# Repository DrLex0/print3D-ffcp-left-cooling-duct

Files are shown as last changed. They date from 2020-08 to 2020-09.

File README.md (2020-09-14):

# FlashForge Creator Pro left single extruder fan duct
*Cooling duct for the left extruder of the FlashForge Creator Pro and similar 3D printers (formerly thing:2436915)*

### License
[Creative Commons - Attribution](https://creativecommons.org/licenses/by/4.0/)

### Attribution
This is a remix of my own [‘FlashForge Creator Pro front dual fan duct’](https://github.com/DrLex0/print3d-ffcp-dual-cooling-duct).

### Gallery

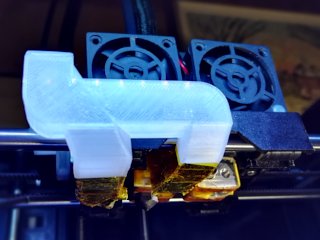
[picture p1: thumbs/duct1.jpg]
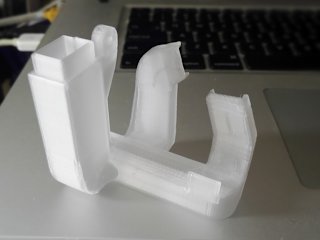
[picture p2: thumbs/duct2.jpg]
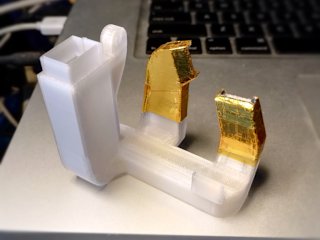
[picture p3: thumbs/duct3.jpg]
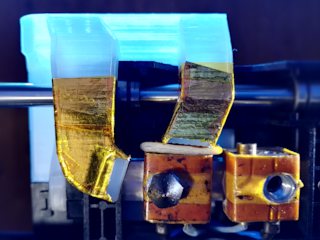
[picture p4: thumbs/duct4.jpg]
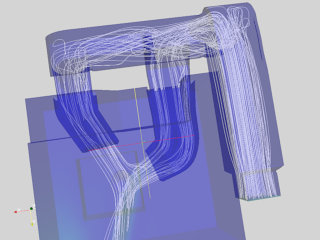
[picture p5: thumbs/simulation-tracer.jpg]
Simulation
[🔎](images/duct1.jpg) [🔎](images/duct2.jpg) [🔎](images/duct3.jpg) [🔎](images/duct4.jpg) [🔎](images/simulation-tracer.png)

## Description and Instructions

This is the single-extrusion alternative to my [dual duct](https://github.com/DrLex0/print3d-ffcp-dual-cooling-duct). I only do a dual extrusion about once every 100 prints, and I figured it is a bit pointless to have the dual duct blow air at the inactive (and usually unscrewed) nozzle all the time. It makes more sense to also direct this air at the active nozzle. By blowing air from two directions, this design reduces the ‘shadow’ problem both the stock duct and my dual duct suffer from, and cools more equally from all sides. If you're only going to print with one extruder, this duct will give you the best quality. Of course this does not make the dual duct obsolete: you still need it to get proper cooling on dual extrusions.

Mind that the shadow problem is not completely eliminated. Overhangs at the rear and right will still be cooled less effectively because the air cannot reach their undersides. One way to work around this is to print extra walls behind such overhangs to reflect the airflow back towards them. In most cases this will be unnecessary however, but keep it in mind for those prints that need to be really perfect.
(Someday I might try to update the design to have opposite exhausts for symmetrical cooling but this will obviously require big changes.)

This duct unfortunately is not plug-and-play. You must read the **Using** section. If you don't, your prints will likely fail, you have been warned.

Quite a bit of time and effort went into designing this. If you want to show some appreciation, [there are some tipping options on my site](https://www.dr-lex.be/about/#contact).

This duct has not been merely designed in a wet-finger guessing way. It has been run through several dozens of iterations, the last of which were validated with computer simulations. See the ‘How I Designed This’ section for more details.

### Pre-printing: check nozzle height

There are two models to choose from. To determine which one you need, do the following test. *Move the bed against the nozzles (as if you are going to use the levelling sheet), then bring the carriage forward and measure the distance between the bed surface and the cradle as shown in the photo.*

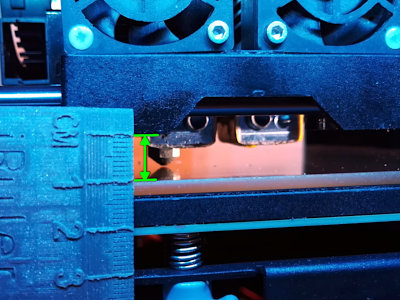
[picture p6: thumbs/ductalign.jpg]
Alignment
[🔎](images/ductalign.jpg)

The regular duct model is designed to be optimal if this distance is **10 mm,** which is normally the case on a standard FFCP. It should also be this way if you aligned the nozzles with [this leveler](https://www.thingiverse.com/thing:1582720).

The ‘x1’ model is for when this distance is **11 mm.** This is likely the case if you installed Micro Swiss all-metal hot-ends and followed their instructions exactly.

If your nozzles are at a considerably different height, you should consider realigning them. If that's not possible, your only option is to modify the duct model.

### Printing

As with the dual duct or any duct whatsoever, you must print this in a **heat-resistant material** because it is very close to the heater block, moreover this duct has even more material near the heated bed. Do *not* print it in PLA. I recommend **ABS** although even that may not be sufficiently heat-resistant on its own during ABS or PETG prints. If you are able to print in polycarbonate, it is probably the best option if you often print with the bed above 100°C or the extruders at 230°C or more. An ABS printed duct will do fine however if you add extra insulation (see *post-printing* section).

This is designed to be printed with an extrusion width of 0.4 mm such that all structures have at least 2 perimeters. The recommended layer height is 0.2 mm. Thinner layers will of course also be OK, and might be beneficial for strength when printing in ABS.

Same remark as for the dual duct: do not enable supports, they could block the inner passages. The model is designed such that it will print well without supports in the orientation of the STL file, i.e., with the inlet pointing upwards.
I recommend enabling cooling while printing the top layer of the main vent and the upper tip of the left exhaust (for this purpose the stock duct should suffice).
Infill doesn't matter much if your slicer is configured to always print small areas solid. If unsure, set infill to 100% for the entire print.

### Post-Printing

**Preparing the duct for mounting**

You should ream the little hole next to the mounting screw hole with a 2 mm drill bit. Otherwise you'll probably have a hard time mounting the duct onto the carriage.

**Protecting the duct against heat**

Even if you printed the duct in ABS, it still is very close to the heater block and the exhausts *will* deform if the duct is exposed to high temperatures for more than just a few minutes while the fan is off or running at very low speed. If the exhausts deform, the duct will no longer work optimally. You should therefore consider applying some thermal insulation to the exhausts, especially if you print with ABS or PETG.

As shown in the photos, I use some NASA-style insulation that consists of a layer of self-adhesive aluminium foil, with a layer of kapton tape on top. To be really sure, I applied this twice at the tips of the exhausts. It is time-consuming to apply this but is well worth it because it has proven to be extremely effective. If you have only one of those materials, I believe a few layers of just aluminium or just kapton will also do the trick.

There are a few cases in which you might get away without insulation:
* If you're only going to print PLA or other filaments that do not require extruder temperatures above 210°C and no bed temperatures above 80°C.
* If you always enable the cooling fan at (near-)maximum speed. This will keep the duct itself cooled and it won't deform. However if you only enable the fan after the first few layers (as you should), then you still risk damaging the duct when printing something large because the duct will remain uncooled during those long first layers.
* If your heater blocks have much better thermal insulation than mine.

### Installing
A thin strip of rubber (like a piece of bicycle tire) under the little mounting tab can help to avoid that the duct vibrates and rattles.

If you have an older printer and yet have to install the blower fan, you may need to print the [fan mounting bracket](https://www.thingiverse.com/thing:2086927) first.

### Using
First of all if you're going to do a long print with the fan disabled entirely, remove the duct to avoid that it will deform, especially if you're printing at very high temperatures, e.g. polycarbonate. Even if you applied thermal insulation, you should still remove the duct if unused during long prints.

Next, very important: don't just print and try to use this duct, it unfortunately is not that simple. **This duct is almost unusable if you cannot control fan speed.** You risk getting very poor layer adhesion in the lower part of your print, and fast-printed parts like infill may detach already during printing. In other words, your print will fall apart. To avoid this, you must reduce fan speed in a specific manner. Unfortunately **fan speed cannot be controlled on an unmodified FFCP,** which I find the largest shortcoming of this printer by far. Modifications are required, below I explain how you can get variable fan speed after all.

Due to effects described below (see ‘Background info’ if you're interested), you must:
* only enable the fan after the second or third layer,
* start out with the fan running at no more than 20% speed,
* gradually increase fan speed over the course of the first few millimeters of the Z-axis until the desired maximum (in my case 50% is usually more than enough).

Being able to control fan speed is the only practical way to get optimal cooling with this duct (actually with any duct for that matter). Variable speed is also essential for getting good results with filaments like PETG, which require a tiny bit of cooling for best results. You may also be surprised to hear that I always enable the fan on ABS prints albeit at very low speed, which does improve quality without ruining layer adhesion. Also, after installing an all-metal hot-end with hardened steel nozzle, I noticed I need much less cooling which made it essential to be able to throttle the fan.

### How to obtain variable fan speed
Your software might make it seem as if you can vary the speed of the fan, but this is a *lie.* None of the printers that use the MightyBoard design like the FFCP and clones, can control fan speed without modifications. The MightyBoard can only toggle its EXTRA output on and off, hence ramping up the fan won't be possible.

Some options:
* Simplest is to install a [hardware PWM controller](https://www.thingiverse.com/thing:2095862) in between the printer motherboard and the cooling fan. This isn't complicated and the only (optional) permanent modification you need to make to your printer is to drill two tiny holes. You can use an analog controller like the one shown there, or a microcontroller like an Arduino with PWM capable output and a 24V MOSFET to drive the fan. This solution is still cumbersome because you will need to babysit every print at least during its first few layers to slowly ramp up the fan speed.
* Better is to use my [MightyVariableFan system](https://github.com/DrLex0/MightyVariableFan), which will result in fully automatic fan speed control that reacts to G-code fan speed commands with high accuracy. Installing it is more work than mounting a single circuit board, but once you've got it running you will never want to go back.
* Install a recent build of the Sailfish firmware that has the software PWM feature. Speed cannot be changed however during a print and it does not respond to speed arguments in the G-code, making it mostly useless. A pull request exists that allows to build a custom firmware which is able to respond to fan speed commands in G-code, but this can only work if you also compile a custom build of the GPX converter and somehow manage to squeeze Sailfish-compatible G-code with variable fan speeds out of your slicing software. And when you have done all this, the timing of the fan speed changes will still be awful.

**Possible workarounds that do not require a PWM controller**

If you don't want to do the effort to add PWM but still want to use this duct, there are some fallbacks that might avoid total disaster, although they are all inferior to varying the fan speed.

* Simplest is to just stick with the [dual duct](https://github.com/DrLex0/print3d-ffcp-dual-cooling-duct).
* Print much hotter, slowly, and in thin layers to reduce the risk of layer delamination.
* To counteract the typical extruder temperature undershoot when the fan activates at lower layers, you could boost extruder temperature by 10°C about 10 seconds before the fan will engage. In theory this should put the extruder is in its heating regime when the blast of cold air hits it, and the undershoot should be reduced or eliminated. You may then gradually reduce extruder temperature again until the print is about 4 mm tall, but you should keep the temperature higher than when printing without fan. This is obviously cumbersome because you will either have to manually fiddle with the LCD menu to do this, or write a post-processing script to insert extra M104 commands in your G-code at the right places.
* Make a hole in the side of the duct to lower the exhaust pressure. You could use tape to vary the size of this hole hence vary airflow in a clumsy manner. Of course this doesn't avoid the undershoot problem and trying to vary the airflow during a print will be challenging to say the least.

## How I Designed This

### SimScale / OpenFOAM
I considered simulating the duct in OpenFOAM but its learning curve is a bit too steep for something I will only be using once or twice. Therefore I first tried the same trial-and-error methods as for the dual duct. These however proved ineffective: the two interacting airflows made the windmill unusable; blowing onto a water surface or a layer of dry sand was also pointless because these methods constrain the test to a 2D surface. (By the way, be extremely careful if you would ever cover the glass bed in your printer with sand. Due to static charge build-up, the sand is likely to jump upwards at the moment you remove the glass plate. It is a very cool physics demonstration but getting the sand out of all the nooks and crannies of your printer is not very cool.)

In the end I did simulate the duct using [SimScale](https://www.simscale.com/), which offers a web interface on top of OpenFOAM for CFD simulations, so this eliminates most of the learning curve. Moreover it is entirely free for public community projects (with a simulation time budget of 3000 hours). You can find the public project [here](https://www.simscale.com/projects/DrLex/ffcp_left_extruder_cooling_duct/).
I ended up performing some 15 different simulations. I couldn't imagine printing and manually testing all those prototypes, so the simulations proved invaluable. I did have some problems getting the STL model imported but in the end I found out how to properly do it, and I can conclude that SimScale is really great.

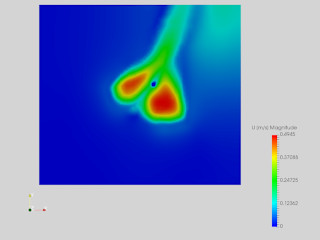
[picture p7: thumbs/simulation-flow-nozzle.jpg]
Simulation 1
[🔎](images/simulation-flow-nozzle.png)

*Airflow velocity around the tip of the nozzle. It is impossible to get a perfectly uniform flow field with only two exhausts, but this is about the best I could get within the constraints of this design.*

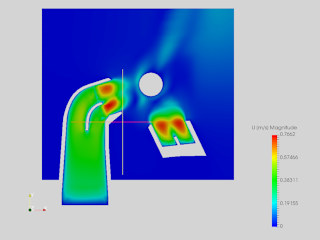
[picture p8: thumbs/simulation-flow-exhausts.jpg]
Simulation 2
[🔎](images/simulation-flow-exhausts.png)

*Flow in the exhausts. Getting this well-balanced was not trivial.*

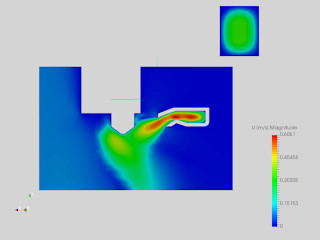
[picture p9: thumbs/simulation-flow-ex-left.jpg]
Simulation 3
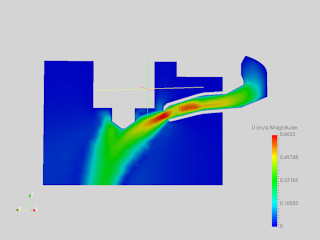
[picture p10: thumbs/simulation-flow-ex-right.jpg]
Simulation 4
[🔎](images/simulation-flow-ex-left.png) [🔎](images/simulation-flow-ex-right.png)

*Flow cross-sections of the left and right exhausts.*

### Validation

The following photos show a comparison of my 55° [mushroom test](https://www.thingiverse.com/thing:2005832) on a PLA print between this duct, the v6 dual duct, and the stock duct. The result from the stock duct looks more decent than what I expected from watching it being printed: it was curling up so badly at times that I feared I would need to abort the print. Somehow the upper layers managed to push down the curls again, but it still looks ugly. Even despite the fact that this was tested with the first version of this new duct which was not anywhere as good as the latest version, the result shows almost no deformations and it has a near-flat top surface. (Note: you won't be able to get this kind of result with the stock nozzles, especially not if they have been worn out. This was printed with a more pointy Micro Swiss hardened steel nozzle which allows to print steeper overhangs than a nozzle with a flat underside.)

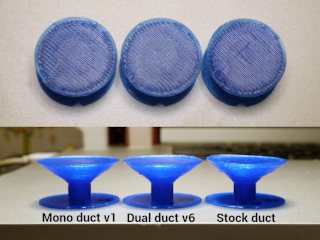
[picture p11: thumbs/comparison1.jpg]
Comparison 1
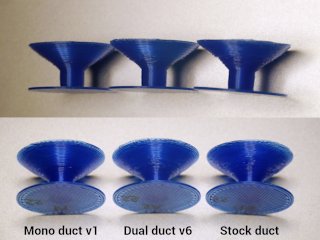
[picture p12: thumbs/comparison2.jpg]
Comparison 2
[🔎](images/comparison1.jpg) [🔎](images/comparison2.jpg)

## Background info: why is throttling the fan necessary?
There are two things at play here. First, the PID controller implementation in the Sailfish firmware is very bad at reacting to temperature drops. The reaction is way too slow therefore if something causes the extruder temperature to suddenly drop, there will be a severe temperature undershoot and part of the print will be printed too cold; layer adhesion will be compromised.

Second, during the first layers of the print, both the extruder and the duct are very close to the bed. This causes the air to ‘bounce,’ forcing it between the bed and heater block, greatly increasing overall airflow. The air hitting the heater block causes the extruder to lose heat, which triggers the PID undershoot problem. Moreover even if the undershoot would not occur, the material would still get cooled much harder than expected. All ducts suffer from this problem, which is why many poorly designed ducts (like the stock duct) work decently during the lower part of the print but do nearly nothing higher up. My duct is designed to work well at all times, which unfortunately causes it to work too well during the lower layers…

Therefore the fan must be started slowly during the lower layers to avoid the undershoot. Its speed must also be kept lower than usual during approximately the lower ≈3 mm of the print, because that's the region where the ‘bounce’ effect remains significant.

The severity of these issues will depend on your printer model and hot-end type. If you're lucky, you don't need to take countermeasures. In my case for instance, the problems only became significant after installing an all-metal hot-end with hardened steel nozzle.

## Will there be a version of this duct for the right extruder?

**No,** because:

1. The left nozzle is closest to the fan, making it much easier to design a duct with two exhausts blowing at it. I don't see any practical way to make a similar configuration for the right nozzle, not even if the left heater block would be removed. The second exhaust would need to make a wide curve around the back, making it large, heavy, and very difficult to print.
2. If you mostly print with one extruder and want to remove the heavy unused stepper motor to reduce ringing artifacts on single-nozzle extrusions, it is way easier to remove and reinstall the right stepper. (You do need to put [something](https://www.thingiverse.com/thing:2474664) in place to trigger the X endstop.)

## Updates
### 2017/07/16: v1
First version.

### 2017/07/26: v2
I noticed that the first version blew way too much air forward. I did most of my tests with the duct in free air, and neglected the fact that when mounted, the airflow would be inclined to get sucked against nearby structures. This did happen and it caused the heater and nozzle to struggle to maintain their temperature. This version improves upon this with a funky new exhaust design, and should also better aim its airflow in the horizontal plane.

**Small update 2017/08/05: v2b**
This is the same design but with a few minor changes that should make it slightly more robust, and also easier to mount with less risk of it cracking.

### 2017/10/21: v3
Almost a complete redesign, the result of performing CFD simulations in SimScale (OpenFOAM). The flows have been balanced and the dead zones have been eliminated. This duct is pretty much guaranteed to be very good. A nice side effect of the optimizations is that the duct is smaller and easier to mount.

### 2020/08/20
Migrate to GitHub, remove last bits of natewin's original source model, and provide Blender file. (No functional changes to the 3D models.)

## Tags
`baffle`, `cfm`, `cooling`, `cooling_duct`, `duct`, `fan_duct`, `FFCP`, `FFCPRo`, `flashforge`, `FlashForge_Dreamer`, `OpenFOAM`, `SimScale`, `simulation`, `upgrade`

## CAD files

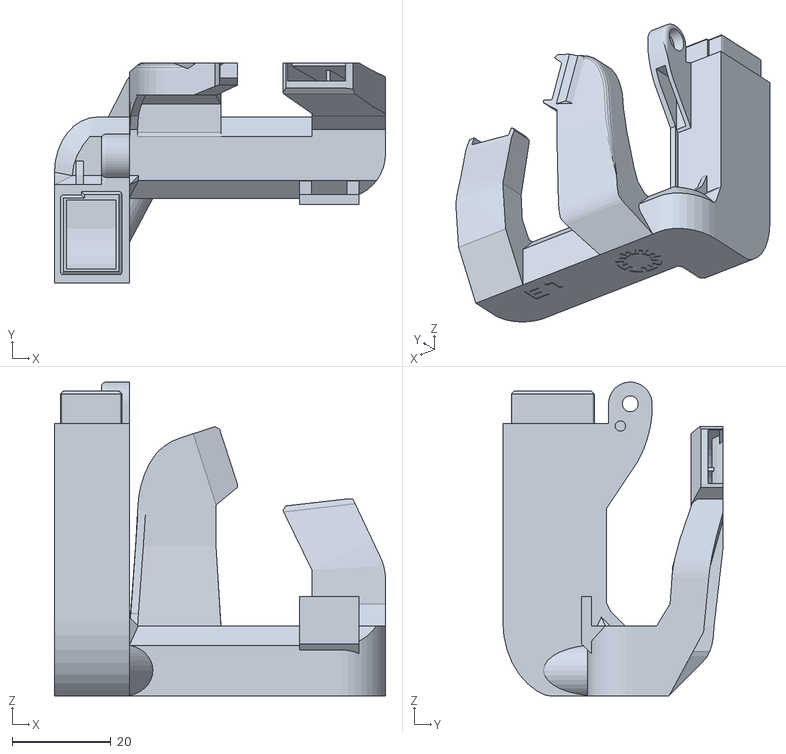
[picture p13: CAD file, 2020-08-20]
FFCP-MonoDuct_v3_x1.stl
67.1 x 44.7 x 63.6

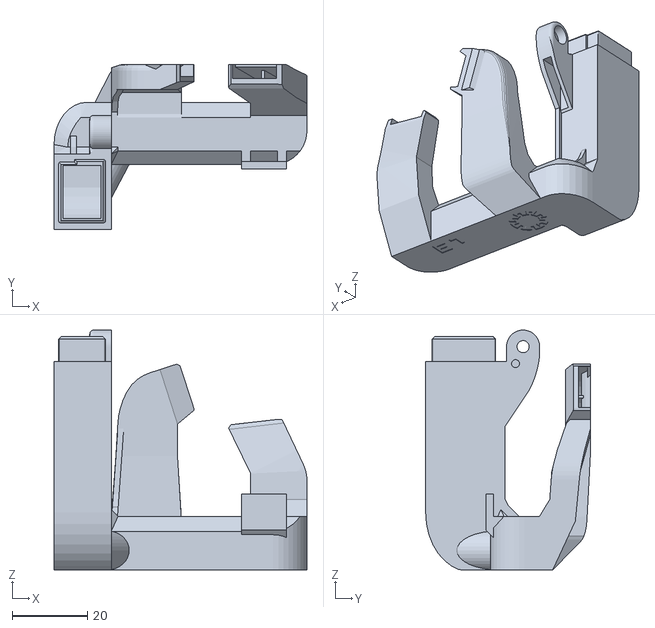
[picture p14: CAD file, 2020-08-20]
FFCP-MonoDuct_v3.stl
67.1 x 43.7 x 63.6

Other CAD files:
FFCP-MonoDuct.blend

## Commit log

2020-08-18 Move to GitHub
    [FFCP-MonoDuct_v3.stl, FFCP-MonoDuct_v3_x1.stl]
2020-08-19 Uniform pre-printing instructions for both duct variations
2020-08-20 Provide Blender source file; remove last remnants of natewin's ‘FFCP DUCT’ model
    [FFCP-MonoDuct.blend, FFCP-MonoDuct_v3.stl, FFCP-MonoDuct_v3_x1.stl]
2020-09-14 More detailed print instructions
